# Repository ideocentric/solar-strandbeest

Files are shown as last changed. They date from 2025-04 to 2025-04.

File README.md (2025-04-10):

# solar-strandbeest

This is the initial design based upon Theo Jansen’s Strandbeest proportions.  

https://www.strandbeest.com

The current version uses 6mm dowels for the main drive chain.  4mm dowels are used to support the body and anchor links.  3mm dowels are used for leg joints.

Currently the design has the following flaws:
1. Center of gravity is a little high and one sided when fully assembled.
2. The leg joints have too much play when using wood only junctions.

The center of gravity issue is more pronounced with the amount of leg play.  This can currently be counter acted by adding weights to the opposite side.

The play in the legs will likely require the use of bearings and screws for the joints instead of plain wood joints.

The overall design is done in 2D for a laser cutter.  However, if desired, much can be extruded by pushing the plane of the components.

Inventory of Items:

1. 4mm bearings: https://www.amazon.com/dp/B082PPQ286
2. 6mm bearings: https://www.amazon.com/dp/B082PSCNKB
3. 150 RPM Motor: https://www.amazon.com/dp/B08B3T8XC5
4. 6V 1W Solar Panel: https://www.amazon.com/dp/B0B8YHP7NR
5. 6mm Wood Dowels: https://www.amazon.com/dp/B07BM99KQV
6. 4mm Wood Dowels: https://www.amazon.com/dp/B0967WF2M5
7. 3mm Wood Dowels: https://www.amazon.com/dp/B0967WZM94

The gear design uses 11 teeth for the small gear and 55 teeth for the large gear.  The general plan was made using the following site:  

https://boxes.hackerspace-bamberg.de/Gears?language=en

The FreeCAD plans include a 5 post internal hub that is swapped out in LightBurn.  FreeCAD does have a way to make gears, but it does not lend itself to 2D design (or I just don’t know how to do it).

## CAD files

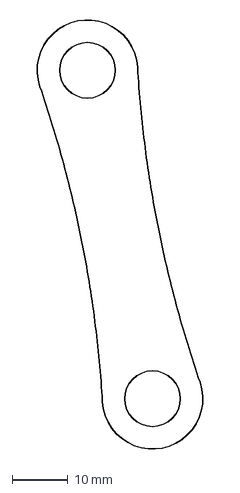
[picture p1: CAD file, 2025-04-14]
v9/v9-m.dxf
31.0 x 78.2 mm

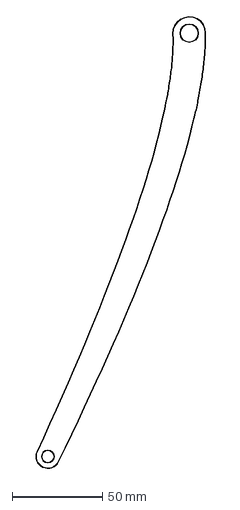
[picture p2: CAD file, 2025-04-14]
v9/v9-k.dxf
94.7 x 251.3 mm

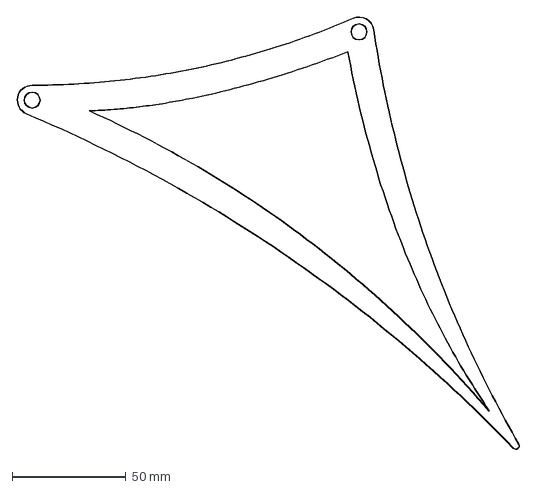
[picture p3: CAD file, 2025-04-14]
v9/v9-ghi.dxf
221.3 x 190.4 mm

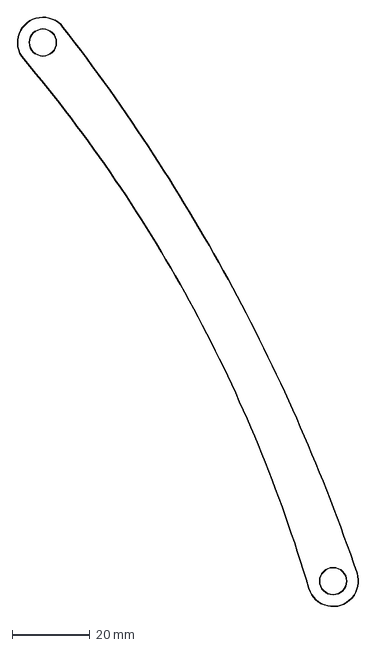
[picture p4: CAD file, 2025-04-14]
v9/v9-f.dxf
88.6 x 152.4 mm

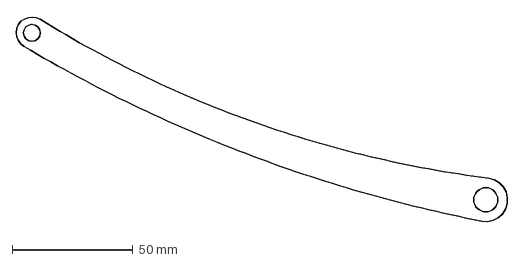
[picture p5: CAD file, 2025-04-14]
v9/v9-j.dxf
203.8 x 85.3 mm

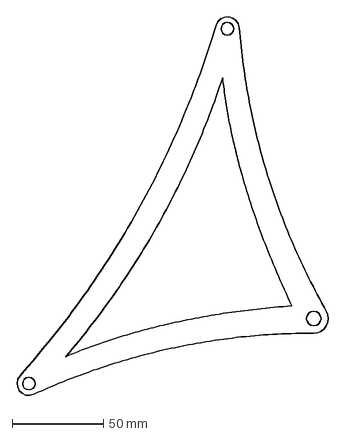
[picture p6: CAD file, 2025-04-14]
v9/v9-bde.dxf
171.8 x 208.8 mm

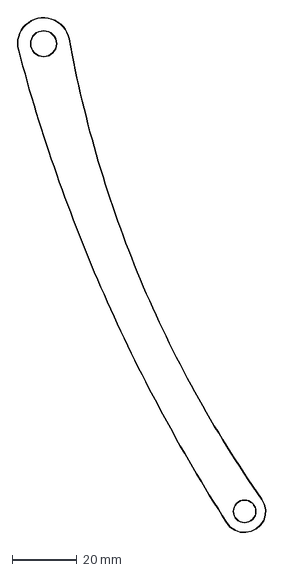
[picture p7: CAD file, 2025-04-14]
v9/v9-c.dxf
77.4 x 159.6 mm

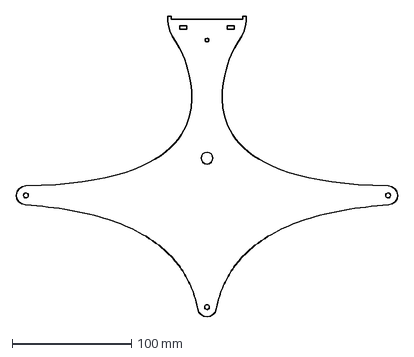
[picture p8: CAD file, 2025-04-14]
v9/v9-a1.dxf
320.2 x 252.0 mm

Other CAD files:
solar-strandbeest-v9.FCStd
solar-strandbeest-4x.FCStd
solar-strandbeest.FCStd

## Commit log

2025-04-10 intial commit
    [solar-strandbeest.FCStd]
2025-04-14 completed base parts
    [solar-strandbeest-4x.FCStd, solar-strandbeest-v9.FCStd, v9-a1.dxf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]
